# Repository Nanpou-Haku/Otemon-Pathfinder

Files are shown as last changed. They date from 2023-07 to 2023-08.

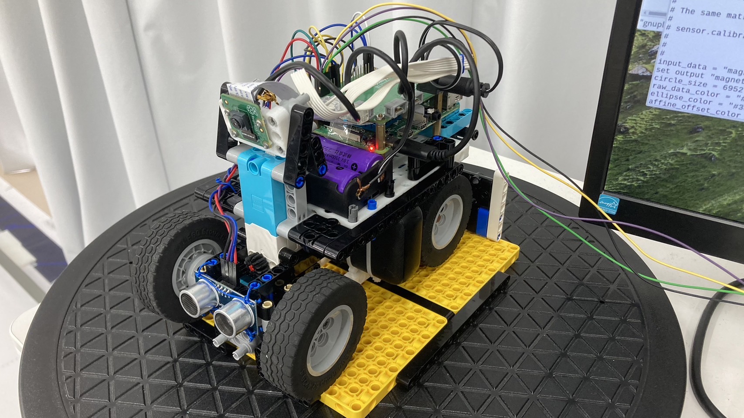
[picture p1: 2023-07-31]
IMG_1999.JPG

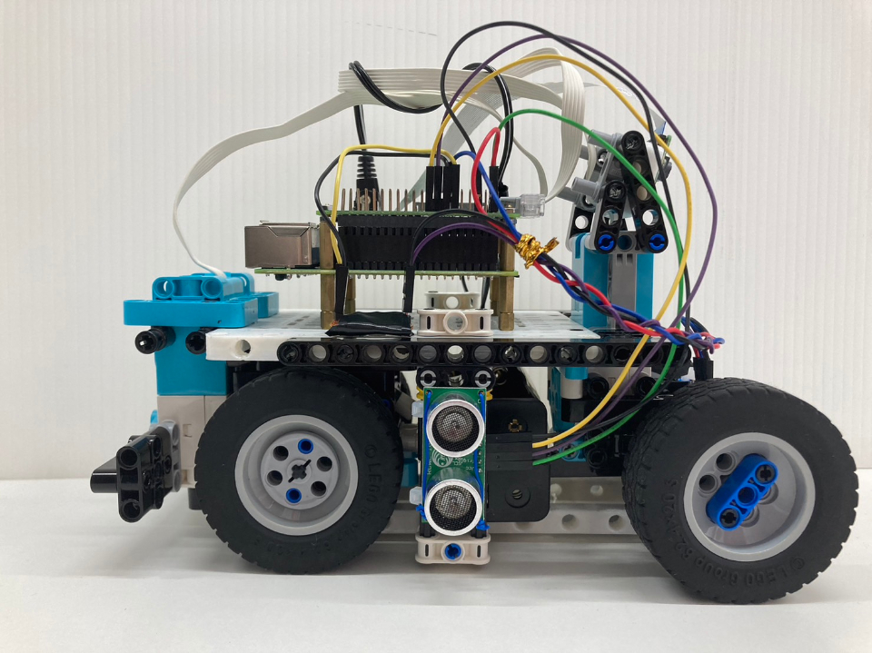
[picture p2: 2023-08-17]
v-photos/robot_right.jpg

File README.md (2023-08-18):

Otemon Pathfinder
====
このレポジトリには、WRO Japan 2023 FUTURE ENGINEERSの自動運転車に関するエンジニアリング資料(すべてのコードや資料など)が含まれています。
___

## 目次

* [自己紹介](#%E8%87%AA%E5%B7%B1%E7%B4%B9%E4%BB%8B)
* [ロボットについて](#%E3%83%AD%E3%83%9C%E3%83%83%E3%83%88%E3%81%AB%E3%81%A4%E3%81%84%E3%81%A6)
* [ハードウェア](#%E3%83%8F%E3%83%BC%E3%83%89%E3%82%A6%E3%82%A7%E3%82%A2)
    * [写真](#%E3%83%AD%E3%83%9C%E3%83%83%E3%83%88%E3%81%AE%E5%86%99%E7%9C%9F)
    * [設計図](#%E8%A8%AD%E8%A8%88%E5%9B%B3)
      * 回路図
      * 構図
      * ステアリング部分
    * [構成の理由](#%E3%81%93%E3%81%AE%E6%A7%8B%E6%88%90%E3%81%AE%E7%90%86%E7%94%B1)
* [ソフトウェア](#%E3%82%BD%E3%83%95%E3%83%88%E3%82%A6%E3%82%A7%E3%82%A2)
  * [使用OS](#%E4%BD%BF%E7%94%A8OS)
  * [プログラミング言語](#%E3%83%97%E3%83%AD%E3%82%B0%E3%83%A9%E3%83%9F%E3%83%B3%E3%82%B0%E8%A8%80%E8%AA%9E)
  * [アルゴリズム](#%E3%82%A2%E3%83%AB%E3%82%B4%E3%83%AA%E3%82%BA%E3%83%A0)
    * [前提](#%E5%89%8D%E6%8F%90%0D%0A)
    * [Open Challenge](#OpenChallenge)
    * [Obstacle Challenge](#ObstacleChallenge)

## 自己紹介

私たちは「Otemon Pathfinder」です。私たちのチームには3人のメンバーがいます。

- 安井　昌望
- 南方　博
- 藤村　昭允
  
（左から）

team_funny

## ロボットについて

私たちのロボットは車体をレゴのパーツで作っており、レゴのパーツで実現することができないものは3Dプリンターで部品を作り、レゴのパーツと互換性を持たせています。

robot

## ハードウェア

| デバイス |  | 用途 |
| :--: | :--:| :--: |
| Raspberry Pi 4B |  | プログラムの実行およびその処理 |
| BuildHat | | LEGOのモーターと接続し、Raspberry Piで制御 |
| Pi Camera V2 |  | 障害物認識、壁検知 |
| HC-SR04 |  | 超音波センサーは壁との距離を計測 前面:衝突を回避 側面:時計回り・半時計回りの判別 |
| Large Angular Motor |　 | 駆動 |
| Medium Angular Motor |  | 操舵 |
| 18650(3.6V, 2600mAh) |  | 電源供給 |
| Switch |  | ロボットの起動 |

### ロボットの写真

| Front | Back |
| -- | -- |
| robot_front | robot_back |

| Left | Right |
| -- | -- |
| robot_left | robot_right |

| Top | Bottom |
| -- | -- |
| robot_top | robot_bottom |

### 設計図
* **回路図**

diagram

* **構図**

blueprint

ディファレンシャルギアはただモーターからタイヤに動力を伝えるのではなく、モーターからリングギアを通して、ピニオンギアやサイドギアへ繋ぎ、タイヤに動力を伝えています。こうすることで、タイヤが両方とも何の負荷もかからずに走行した場合はリングギアが回転し、ピニオンギアは動きません。しかし、どちらか片方が動かない、もしくは負荷がかかった場合にはピニオンギアが作動し、もう片方のタイヤを余分に回転させます。こうすることで**タイヤの回転差を調整し、スムーズな走行が可能**になり、コートでカーブする際に効果を発揮します。

differential gear 

（ディファレンシャルギア）

* **ステアリング部分**

steering

### この構成の理由

1. トライ＆エラーのしやすさ：私たちはRaspberry Piの高い拡張性を活用することで、様々な種類のカメラモジュール、I2C接続センサー、GPIO制御を試しました。こうした豊富な選択肢を通じて、異なる手法やアプローチを試行し、最適解を求めていくことを可能にしました。

2. 最適な互換性：LEGOを選んだ理由は、**組み立てが容易で、ロボットの修理や新しい機構の追加が素早く行える**ためです。加えて、多様なパーツが利用でき、アイデアを迅速に形にできます。さらに、Raspberry Pi BuildHatを使用してLEGO SpikeのモーターをRaspberry Piで制御できる**高い互換性**があり、3Dプリンターを活用してLEGOと互換性のあるカスタムパーツを製作できるため、理想のロボットを作り上げるための自由度が高めました。

3. エネルギー効率とコスト：Lidarセンサーの代わりにカメラや超音波センサーを使っている理由は、**コストパフォーマンスや主な焦点である軽量設計**に貢献していること、通常、Lidarセンサーに比べ、カメラや超音波センサーは**低い消費電力**であり、エネルギー効率が良いです。

4. 安定した電力供給と柔軟性：18650電池4本をBuildHatに接続し、電源を供給することにしました。**スイッチを一度オンにするだけ電源を供給することができ、バッテリーの交換や管理が容易に行えるため、柔軟な運用が可能で、負荷の高い処理を実行する際にも安定した電力供給が保たれ、長時間の稼働においても安定性**が保たれることが期待されます。

## ソフトウェア

### 使用OS

私たちは既存のDebian BusterがベースとなったRaspberry Pi OSを使用しています。

### プログラミング言語

私たちのコードはすべて、Pythonで書かれています。

### アルゴリズム

* ### 前提

前提として、カメラの解像度は画像処理に大きく影響します。Pi Camera V2の場合、解像度と画素数は以下の表のようになります。

| 解像度 | 画素数 |
| :--: | :--: |
| 1920 × 1080 | 207万画素 |
| 1280 x 720 | 92万画素 |
| 640 x 480 | 30万画素 |

この表から分かるように、高解像度の場合、データ量が多く、リアルタイムで処理する際に処理に負荷がかかります。Future Engineersでは、3分以内に3周する速度とオブジェクトの認識の精度が求められるため、高解像度であると、処理能力が追いつかず、FPS(フレームレート)が下がり、画像データの更新が遅くなります。Open Challengeでは障害物を避ける必要がなく、壁のみの画像処理と超音波によるP制御より、解像度は640×480とし、Obstacle Challengeでは障害物と壁の画像処理が必要であるため、320×240としています。

* ### OpenChallenge

Open Challengeは、トラックに障害物がなく、中央の壁が変化することにより、セクションにより壁と壁の幅が変化するため、適応しながら、3周をするミッションです。このミッションの達成方法として、以下のアルゴリズムを考えました。

1. 障害物がないため、壁のしきい値の最小値と最大値の範囲を定義し、真ん中から下部をROI(関心領域)抽出・マスク処理(二値化)をしたあと、そのデータにオープニング処理(ノイズ除去、特徴抽出)を施す。

2. オープニング処理を施した画像の輪郭から壁の最大面積を算出する。

3. 画像の中央（ROI抽出した画像の左側、右側を切り取る）のみにし、中央に表示される壁の面積がある一定の値を超えるまで、ロボットの左右にある超音波センサー(HC-SR04)で左右の壁のちょうど中央になるようにP制御を用いて、トレースをする。

4. 中央に表示される壁の面積がある一定の値を超える条件が満たされた時、壁に近いので、左右の超音波センサーのうち、どちら側が壁からの距離が遠いか比較し、判別する。

5. 壁からの距離が遠い方で時計回りか反時計回りか判別できるので、その判別結果を用いて、時計回りなら右に、反時計回りなら左に曲がるようにステアリングを操作する。(この時、時計回りか反時計回りかを記憶し、２回目以降にその判断結果を用いる)

6. 1.~5.の動作を3周するまで繰り返す。

* ### ObstacleChallenge

Obstacle Challengeは、障害物を避けながら、3周をするミッションです。このミッションの達成方法として以下のアルゴリズムを考えました。

1. 赤色と緑色のしきい値の最小値と最大値の範囲を定義し、マスク処理をしたあと、そのデータにオープニング処理を施す。

2. オープニング処理を施した画像の輪郭から赤色と緑色の最大面積とその面積の重心を算出する。

detect

content

3. その最大面積を評価し、赤と緑、どちらの面積の方が大きいか、その面積は十分に大きいかという条件を満たすか判定する。(算出された面積が大きければ、大きいほどロボットに近いところにあるといえる)

4. ロボットの目の前にオブジェクトがある時(面積がある一定の値以上の条件)オブジェクトの色に応じて、ステアリングを操作し、回避を行う。

5. ここで、三分割されたマスク画像について、2.で算出された重心が赤なら左側の領域、緑なら右側の領域に入った時、オブジェクトは回避できたと判断する。

6. 4.、5.の間にかかった時間（回避に要した時間)を算出しておき、それを元に今度は逆向きにステアリングを操作し、ロボットを元の位置に戻す。

7. 1.~6.の動作を3周するまで繰り返す。

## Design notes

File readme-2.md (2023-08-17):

Otemon Pathfinder
====
このレポジトリには、WRO Japan 2023 FUTURE ENGINEERSの自動運転車に関するエンジニアリング資料(すべてのコードや資料など)が含まれています。
___

## 目次

* [自己紹介](#%E8%87%AA%E5%B7%B1%E7%B4%B9%E4%BB%8B)
* [ロボットについて](#%E3%83%AD%E3%83%9C%E3%83%83%E3%83%88%E3%81%AB%E3%81%A4%E3%81%84%E3%81%A6)
* [ハードウェア](#%E3%83%8F%E3%83%BC%E3%83%89%E3%82%A6%E3%82%A7%E3%82%A2)
    * [写真](#%E3%83%AD%E3%83%9C%E3%83%83%E3%83%88%E3%81%AE%E5%86%99%E7%9C%9F)
    * [設計図](#%E8%A8%AD%E8%A8%88%E5%9B%B3)
      * 回路図
      * 構図
      * ステアリング部分
    * [構成の理由](#%E3%81%93%E3%81%AE%E6%A7%8B%E6%88%90%E3%81%AE%E7%90%86%E7%94%B1)
* [ソフトウェア](#%E3%82%BD%E3%83%95%E3%83%88%E3%82%A6%E3%82%A7%E3%82%A2)
  * [使用OS](#%E4%BD%BF%E7%94%A8OS)
  * [プログラミング言語](#%E3%83%97%E3%83%AD%E3%82%B0%E3%83%A9%E3%83%9F%E3%83%B3%E3%82%B0%E8%A8%80%E8%AA%9E)
  * [アルゴリズム](#%E3%82%A2%E3%83%AB%E3%82%B4%E3%83%AA%E3%82%BA%E3%83%A0)
    * [前提](#%E5%89%8D%E6%8F%90%0D%0A)
    * [Open Challenge](#OpenChallenge)
    * [Obstacle Challenge](#ObstacleChallenge)

## 自己紹介

私たちのチーム「Otemon Pathfinder」には3人のメンバーがいます。

- 安井　昌望
- 南方　博
- 藤村　昭允
  
（左から）

team_funny

## ロボットについて

私たちのロボットは、ハードウェアもソフトウェアも無駄のない設計にこだわりました。
ハードウェアの面では汎用的なレゴのパーツにより高いカスタマイズ性を担保しつつ、専用設計したパーツを組み合わせることで無駄がない構造の実現に成功しました。
ソフトウェアの面では再利用性のあるクラスにより汎用的で非冗長的な処理をしつつ、比較的単純なアルゴリズムで保守性と可読性のあるコードの実現に成功しました。

robot

## ハードウェア

| デバイス |  | 用途 |
| :--: | :--:| :--: |
| Raspberry Pi 4B |  | プログラムの実行およびその処理 |
| BuildHat | | LEGOのモーターと接続し、Raspberry Piで制御 |
| Pi Camera V2 |  | 障害物認識、壁検知 |
| HC-SR04 |  | 超音波センサーは壁との距離を計測 前面:衝突を回避 側面:時計回り・半時計回りの判別 |
| Large Angular Motor |　 | 駆動 |
| Medium Angular Motor |  | 操舵 |
| 18650(3.6V, 2600mAh) |  | 電源供給 |
| Switch |  | ロボットの起動 |

### ロボットの写真

| Front | Back |
| -- | -- |
| robot_front | robot_back |

| Left | Right |
| -- | -- |
| robot_left | robot_right |

| Top | Bottom |
| -- | -- |
| robot_top | robot_bottom |

### 設計図
* **回路図**

diagram

* **構図**

blueprint

ディファレンシャルギアはただモーターからタイヤに動力を伝えるのではなく、モーターからリングギアを通して、ピニオンギアやサイドギアへ繋ぎ、タイヤに動力を伝えています。こうすることで、タイヤが両方とも何の負荷もかからずに走行した場合はリングギアが回転し、ピニオンギアは動きません。しかし、どちらか片方が動かない、もしくは負荷かかかった場合にはピニオンギアが作動し、もう片方のタイヤを余分に回転させます。こうすることで**タイヤの回転差を調整し、スムーズな走行が可能**になり、コート上でカーブする際に効果を発揮します。

differential gear 

（ディファレンシャルギア）

* **ステアリング部分**

steering

### この構成の理由

1. トライ＆エラーのしやすさ：私たちはRaspberry Piの高い拡張性を活用することで、様々な種類のカメラモジュール、i2c接続センサ、gpio制御を試し、多くの手法から最適解を求めていくことを可能にしました。

2. 最適な互換性：LEGOを選んだ理由は、**組み立てが容易で、ロボットの修理や新しい機構の追加が素早く行える**ためです。加えて、多様なパーツが利用でき、アイデアを迅速に形にできます。さらに、Raspberry Pi BuildHatを使用してLEGO SpikeのモーターをRaspberry Piで制御できる**高い互換性**があり、3Dプリンターを活用してLEGOと互換性のあるカスタムパーツを製作できるため、理想のロボットを作り上げるための自由度を高めました。

3. エネルギー効率とコスト：Lidarセンサーの代わりにカメラや超音波センサーを使っている理由は、**コストパフォーマンスや主な焦点である軽量設計**に貢献していること、通常、Lidarセンサーに比べ、カメラや超音波センサーは**低い消費電力**であり、エネルギー効率が良いです。

4. 安定した電力供給と柔軟性：18650電池4本を BuildHatに接続し、電源を供給することにしました。**スイッチを一度オンにするだけで電源を供給することができ、バッテリーの交換や管理が容易に行える**ため、**柔軟な運用**が可能で、**電力供給の安定性が増し、長時間稼働する際にも安定性**が保たれることが期待されます。

## ソフトウェア

### 使用OS

私たちはRaspberry Pi OSを使用しています。

### プログラミング言語

私たちのコードはすべて、Pythonで書かれています。

### アルゴリズム

* ### 前提

前提として、カメラの解像度は画像処理に大きく影響します。Pi Camera V2の場合、解像度と画素数は以下の表のようになります。

| 解像度 | 画素数 |
| :--: | :--: |
| 1920 × 1080 | 207万画素 |
| 1280 x 720 | 92万画素 |
| 640 x 480 | 30万画素 |

この表から分かるように、高解像度の場合、データ量が多く、リアルタイムで処理する際に処理に負荷がかかります。Future Engineersでは、3分以内に3周する速度とオブジェクトの認識の精度が求められるため、高解像度であると、処理能力が追いつかず、FPS(フレームレート)が下がり、画像データの更新が遅くなります。Open Challengeでは障害物を避ける必要がなく、壁のみの画像処理と超音波によるP制御より、解像度は640×480とし、Obstacle Challengeでは障害物と壁の画像処理が必要であるため、320×240としています。

* ### OpenChallenge

Open Challengeは、トラックに障害物がなく、中央の壁が変化することにより、セクションにより壁と壁の幅が変化するため、適応しながら、3周をするミッションです。このミッションの達成方法として、以下のアルゴリズムを考えました。

1. 障害物がないため、壁のしきい値の最小値と最大値の範囲を定義し、真ん中から下部をROI(関心領域)抽出・マスク処理(二値化)をしたあと、そのデータにオープニング処理(ノイズ除去、特徴抽出)を施す。

2. オープニング処理を施した画像の輪郭から壁の最大面積を算出する。

3. 画像の中央（ROI抽出した画像の左側、右側を切り取る）のみにし、中央に表示される壁の面積がある一定の値を超えるまで、ロボットの左右にある超音波センサー(HC-SR04)で左右の壁のちょうど中央になるようにP制御を用いて、トレースをする。

4. 中央に表示される壁の面積がある一定の値を超える条件が満たされた時、壁に近いので、左右の超音波センサーのうち、どちら側が壁からの距離が遠いか比較し、判別する。

5. 壁からの距離が遠い方で時計回りか反時計回りか判別できるので、その判別結果を用いて、時計回りなら右に、反時計回りなら左に曲がるようにステアリングを操作する。(この時、時計回りか反時計回りかを記憶し、２回目以降にその判断結果を用いる)

6. 1.~5.の動作を3周するまで繰り返す。

* ### ObstacleChallenge

Obstacle Challengeは、障害物を避けながら、3周をするミッションです。このミッションの達成方法として以下のアルゴリズムを考えました。

1. 赤色と緑色のしきい値の最小値と最大値の範囲を定義し、マスク処理をしたあと、そのデータにオープニング処理を施す。

2. オープニング処理を施した画像の輪郭から赤色と緑色の最大面積とその面積の重心を算出する。

detect

content

3. その最大面積を評価し、赤と緑、どちらの面積の方が大きいか、その面積は十分に大きいかという条件を満たすか判定する。(算出された面積が大きければ、大きいほどロボットに近いところにあるといえる)

4. ロボットの目の前にオブジェクトがある時(面積がある一定の値以上の条件)オブジェクトの色に応じて、ステアリングを操作し、回避を行う。

5. ここで、三分割されたマスク画像について、2.で算出された重心が赤なら左側の領域、緑なら右側の領域に入った時、オブジェクトは回避できたと判断する。

6. 4.、5.の間にかかった時間（回避に要した時間)を算出しておき、それを元に今度は逆向きにステアリングを操作し、ロボットを元の位置に戻す。

7. 1.~6.の動作を3周するまで繰り返す。

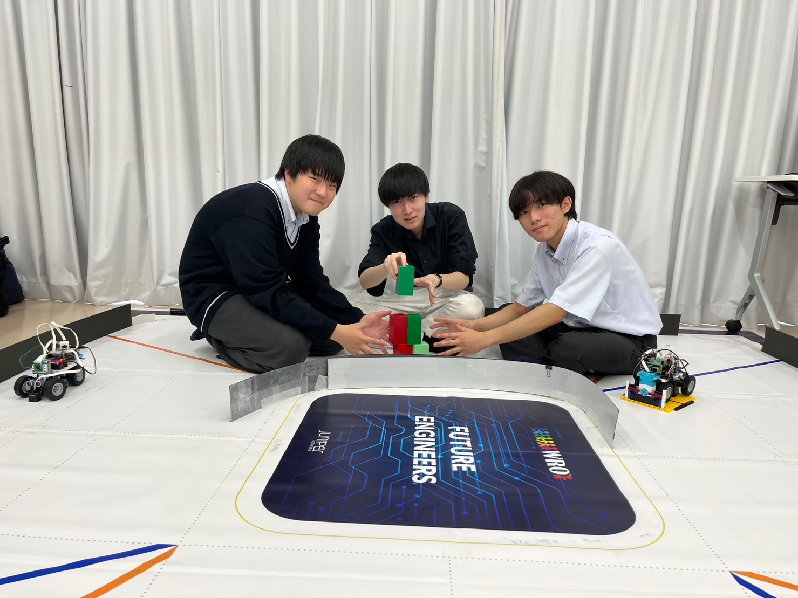
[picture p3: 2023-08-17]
t-photos/team_funny.jpg

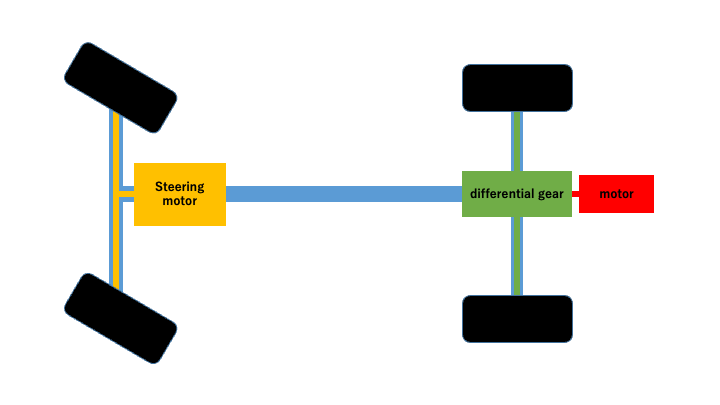
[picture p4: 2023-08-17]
models/robot_blueprint.png

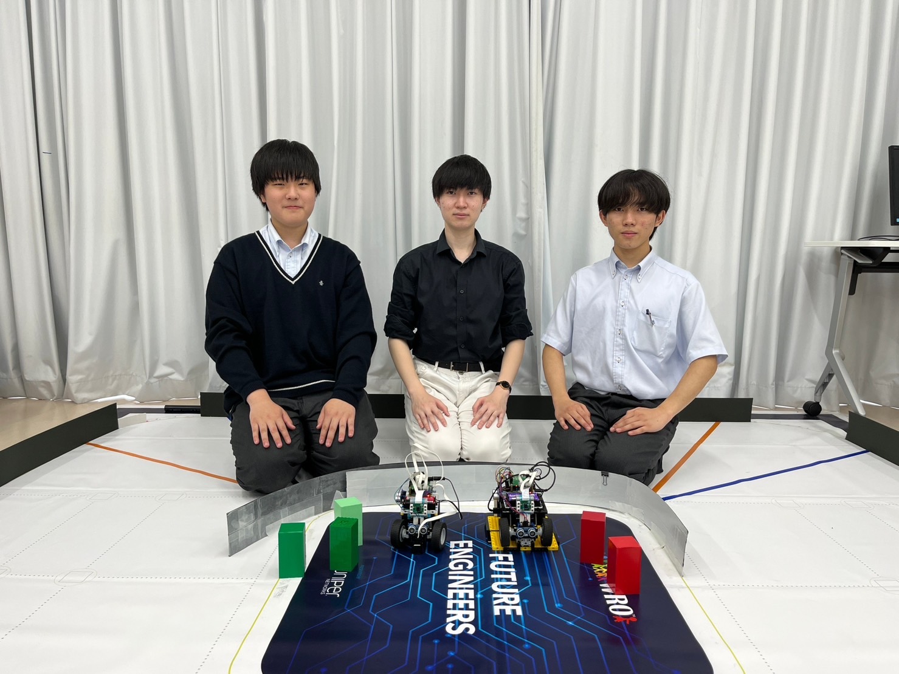
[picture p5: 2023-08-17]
t-photos/team_official.jpg

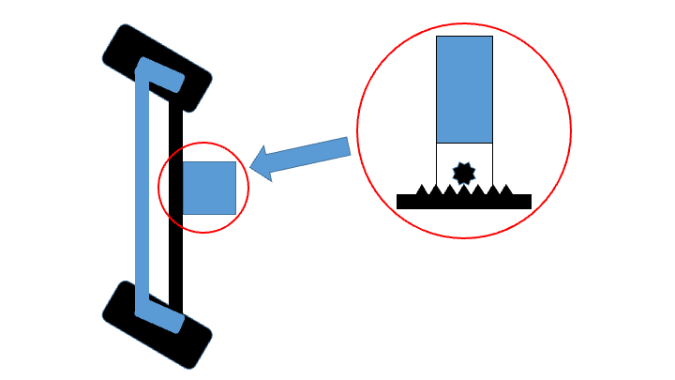
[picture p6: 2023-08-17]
models/robot_steering.png

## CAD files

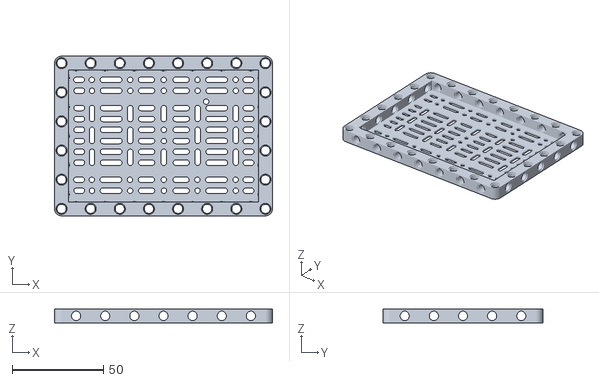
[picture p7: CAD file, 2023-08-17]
models/raspberry-lego-maker-plate_v4.stl
119.8 x 87.8 x 7.75

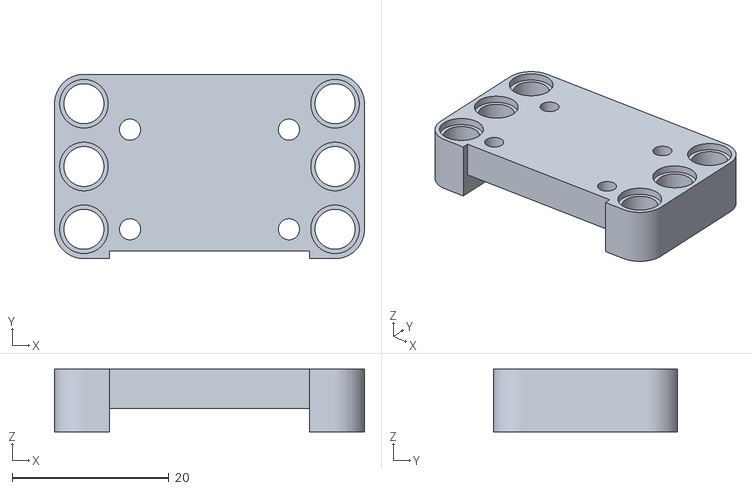
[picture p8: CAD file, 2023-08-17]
models/camera2.stl
39.5 x 23.5 x 8.00

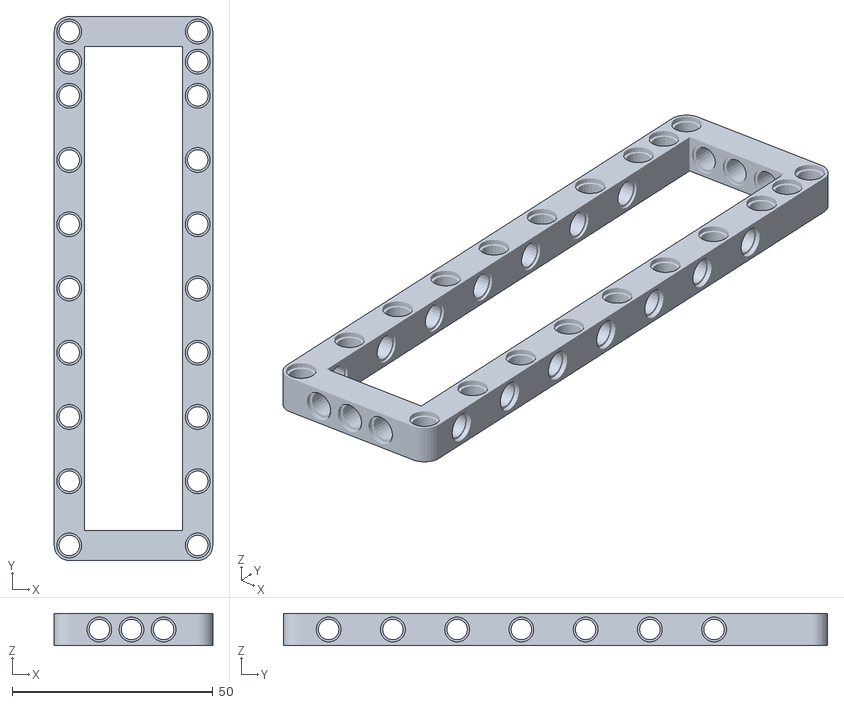
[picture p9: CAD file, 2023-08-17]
models/robot_under.stl
39.5 x 135.5 x 8.00

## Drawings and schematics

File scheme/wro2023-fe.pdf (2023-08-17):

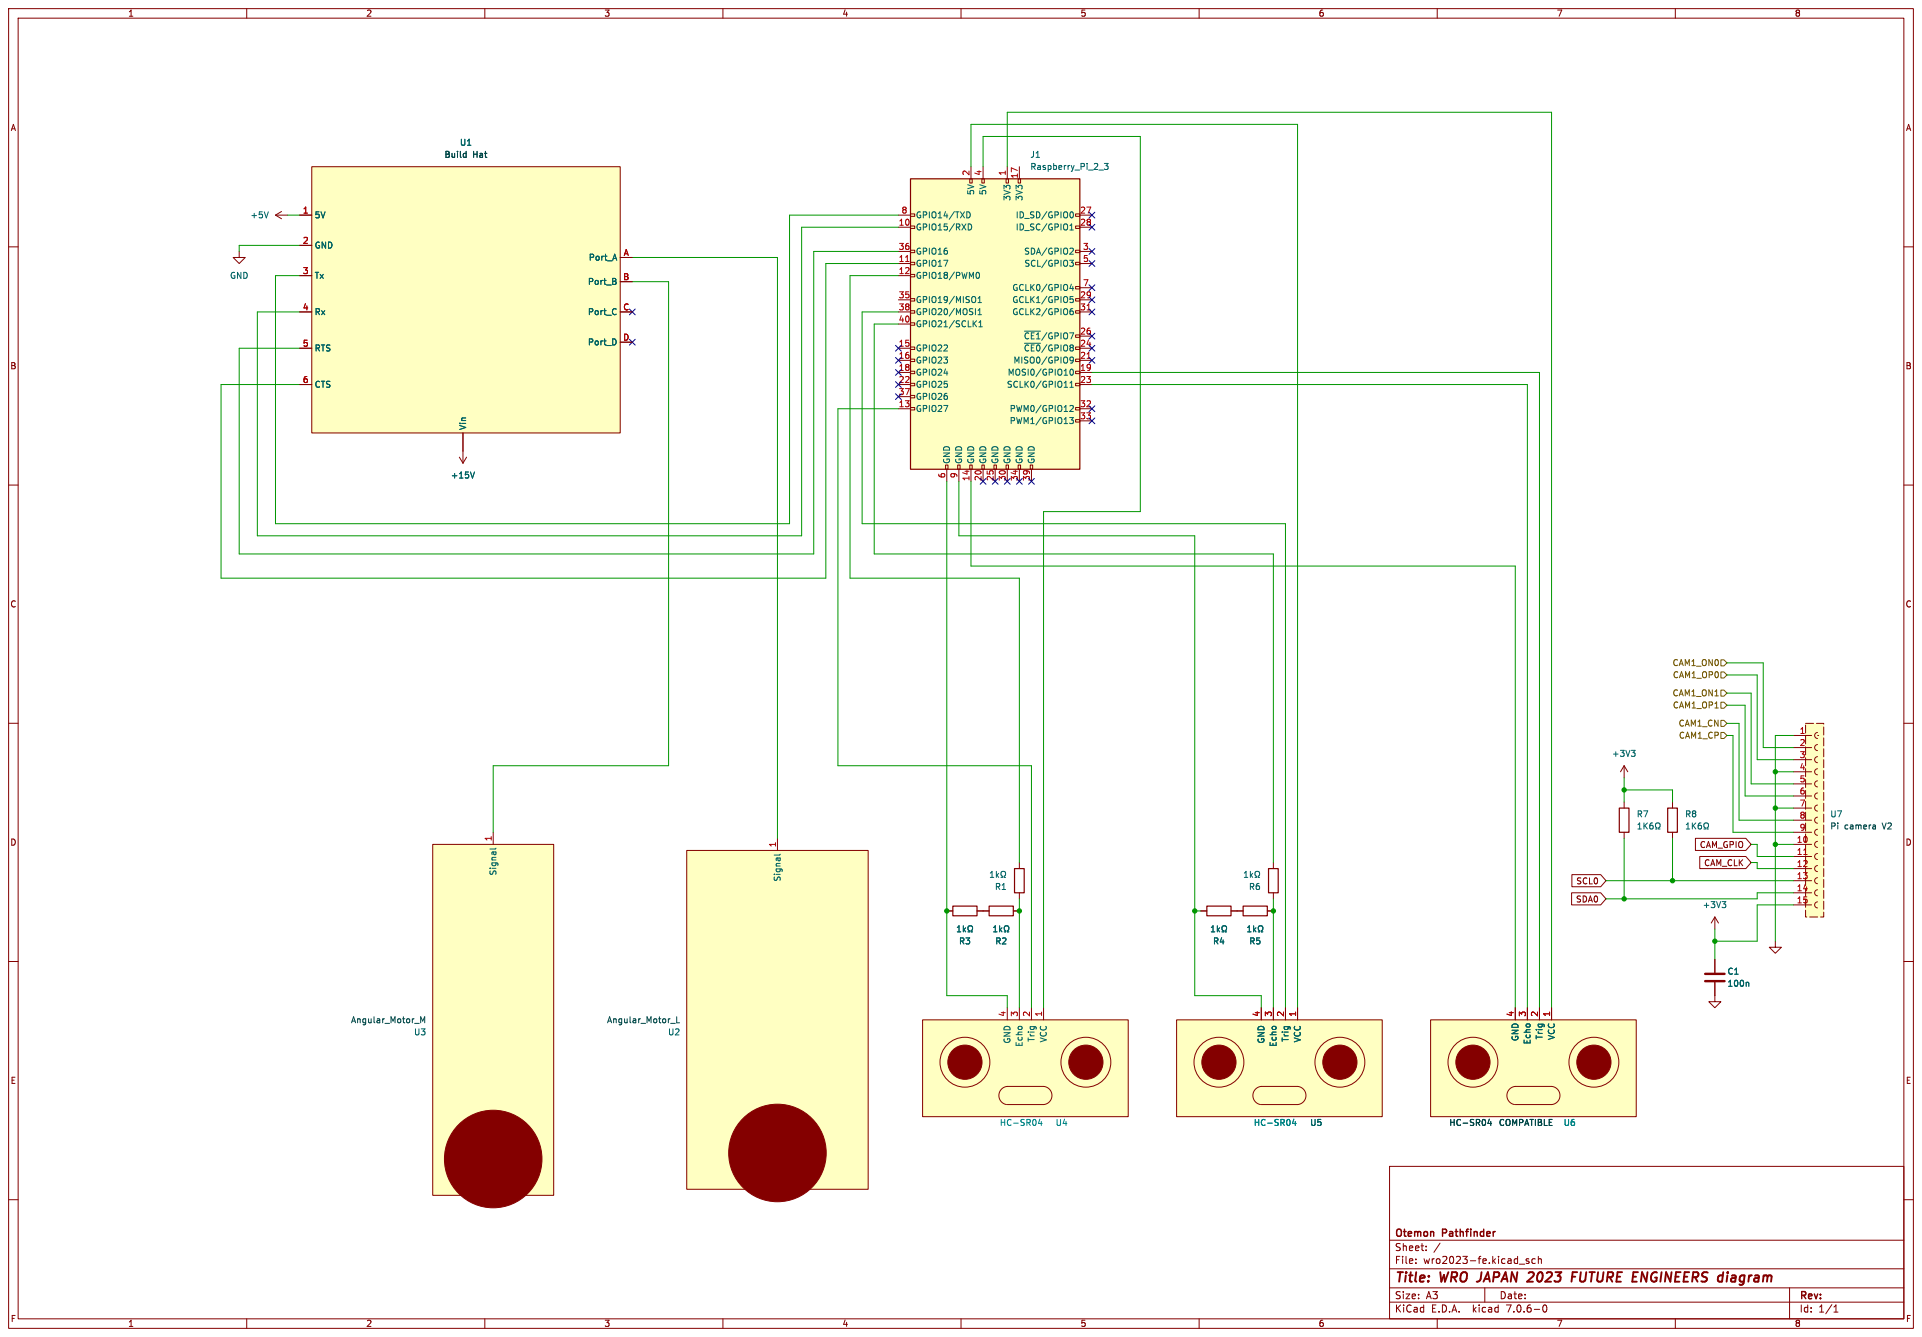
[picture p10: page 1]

Id: 1/1 Title: WRO JAPAN 2023 FUTURE ENGINEERS diagram

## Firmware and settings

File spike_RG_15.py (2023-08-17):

import time
import atexit
import picamera
import picamera.array
import RPi.GPIO as GPIO
from dataclasses import dataclass
import cv2
import numpy as np
from buildhat import Motor, ForceSensor
import copy
import math

@dataclass
class ColorDatas:
    color      : int = 0
    lower      : np.ndarray = None
    upper      : np.ndarray = None
    mask       : np.ndarray = None
    dst        : np.ndarray = None
    dstt       : np.ndarray = None
    res        : np.ndarray = None
    contour    : np.ndarray = None
    hierarchy  : np.ndarray = None
    maxContour : int = None
    area       : int = None
    moments    : dict = None
    
#pin
trig_front = 27
echo_front = 18
trig_side = 20
echo_side = 21

#connect
motor = Motor('A')
steering = Motor('B')
left = -70
right = 70

#color
green = ColorDatas()
red = ColorDatas()
red2 = ColorDatas()
blue = ColorDatas()
black = ColorDatas()

#camera
camera = picamera.PiCamera()
wide, high = (320, 240)
frame = 10

sig_off = 0
dig_on = 0
start = 0
end = 0
total = 0
clock = 0
direction = 0
counter = 0
surf = 0
blue.area = 0
degree = 0

first = True
waitPls = True

poleFlag = False
blueFlag = False
startFlag = False

#Hiroshi
def init():
    GPIO.setwarnings(False)
    GPIO.setmode(GPIO.BCM)              
    GPIO.setup(trig_front, GPIO.OUT)          
    GPIO.setup(echo_front, GPIO.IN)
    GPIO.setup(trig_side, GPIO.OUT)          
    GPIO.setup(echo_side, GPIO.IN)
    
    blue.lower = np.array([104, 85, 0])
    blue.upper = np.array([170, 255, 163])
    blue.color = "blue"
    
    green.lower = np.array([40, 60, 40])
    green.upper = np.array([80, 255, 255])
    green.color = "green"
    
    red.lower = np.array([160, 60, 50])
    red.upper = np.array([179, 255, 255])
    red.color = "red"

    red2.lower = np.array([0, 255, 50])
    red2.upper = np.array([30, 255, 255])   
    red2.color = "red"
    
    black.lower = np.array([0, 0, 0])
    black.upper = np.array([50, 225, 110])
    black.color = "black"
    
    camera.rotation = 180
    camera.resolution = (wide, high)
    camera.framerate = frame
    
def UpdateCamera(stream, kernel):
    #camera
    camera.capture(stream, 'bgr', use_video_port=True)
    hsv = cv2.cvtColor(stream.array, cv2.COLOR_BGR2HSV)
    
    hsvline = cv2.cvtColor(stream.array, cv2.COLOR_BGR2HSV)
    blind = cv2.rectangle(hsvline, (0, 0), (320, 120), (100, 100, 100), -1)
    
    hsvblack = cv2.cvtColor(stream.array, cv2.COLOR_BGR2HSV)
    black_blind1 = cv2.rectangle(hsvblack, (0, 0), (320, 100), (240, 240, 240), -1)
    black_blind2 = cv2.rectangle(black_blind1, (0, 0), (20, 240), (240, 240, 240), -1)
    black_blind3 = cv2.rectangle(black_blind2, (300, 0), (320, 240), (240, 240, 240), -1)
    
    #マスク処理
    green.mask = cv2.inRange(hsv, green.lower, green.upper)
    red.mask = cv2.inRange(hsv, red.lower, red.upper)
    red2.mask = cv2.inRange(hsv, red2.lower, red2.upper)
    red.mask = red.mask + red2.mask
    
    blue.mask = cv2.inRange(hsvline, blue.lower, blue.upper)
    black.mask = cv2.inRange(hsvblack, black.lower, black.upper)
    
    #オープニング
    green.dst = cv2.erode(green.mask, kernel, iterations=1)
    green.dstt = cv2.dilate(green.dst, kernel, iterations=1)
    red.dst = cv2.erode(red.mask, kernel, iterations=1)
    red.dstt = cv2.dilate(red.dst, kernel, iterations=1)
    
    blue.dst = cv2.erode(blue.mask, kernel, iterations=1)
    blue.dstt = cv2.dilate(blue.dst, kernel, iterations=1)
    black.dst = cv2.erode(black.mask, kernel, iterations=1)
    black.dstt = cv2.dilate(black.dst, kernel, iterations=1)
    
    #合成
    green.res = cv2.bitwise_and(stream.array, stream.array, mask=green.dstt)
    red.res = cv2.bitwise_and(stream.array, stream.array, mask=red.dstt)
    
    blue.res = cv2.bitwise_and(stream.array, stream.array, mask=blue.dstt)
    black.res = cv2.bitwise_and(stream.array, stream.array, mask=black.dstt)
    
    #輪郭検出
    green.contour, green.hierarchy = cv2.findContours(green.mask, cv2.RETR_EXTERNAL, cv2.CHAIN_APPROX_SIMPLE)
    red.contour, red.hierarchy = cv2.findContours(red.mask, cv2.RETR_EXTERNAL, cv2.CHAIN_APPROX_SIMPLE)
    
    blue.contour, blue.hierarchy = cv2.findContours(blue.mask, cv2.RETR_EXTERNAL, cv2.CHAIN_APPROX_SIMPLE)
    black.contour, black.hierarchy = cv2.findContours(black.mask, cv2.RETR_EXTERNAL, cv2.CHAIN_APPROX_NONE)
    
    #分割線描画
    cv2.line(green.res, (41, 0), (41,240), (255, 215, 0), 1)
    cv2.line(green.res, (280, 0), (280,240), (255, 215, 0), 1)
    cv2.line(red.res, (41, 0), (41,240), (255, 215, 0), 1)
    cv2.line(red.res, (280, 0), (280,240), (255, 215, 0), 1)

#Fujimura
def situation():
    stream = picamera.array.PiRGBArray(camera)
    kernel = cv2.getStructuringElement(cv2.MORPH_RECT, (3,3))
    UpdateCamera(stream, kernel)
    
    if (len(green.contour) != 0):
        green.maxContour = max(green.contour, key = lambda x: cv2.contourArea(x))
        green.area = cv2.contourArea(green.maxContour)
        green.moments = cv2.moments(green.maxContour)
    
    if (len(red.contour) != 0):
        red.maxContour = max(red.contour, key = lambda x: cv2.contourArea(x))
        red.area = cv2.contourArea(red.maxContour)
        red.moments = cv2.moments(red.maxContour)
    
    if (len(black.contour) != 0):
        black.maxContour = max(black.contour, key = lambda x: cv2.contourArea(x))
        black.area = cv2.contourArea(black.maxContour)
        black.moments = cv2.moments(black.maxContour)
    
    else:
        green.area = 0
        red.area = 0
        black.area = 0
    
def situationBlue():
    stream = picamera.array.PiRGBArray(camera)
    kernel = cv2.getStructuringElement(cv2.MORPH_RECT, (3,3))
    UpdateCamera(stream, kernel)
    
    if (len(blue.contour) != 0):
        blue.maxContour = max(blue.contour, key = lambda x: cv2.contourArea(x))
        blue.area = cv2.contourArea(blue.maxContour)
        blue.moments = cv2.moments(blue.maxContour)
    
    else:
        blue.area = 0
        
    return blue.area
    
def CameraShow(stream, kernel):
    #表示
    cv2.imshow("frame", stream.array)
    cv2.imshow("Green", green.res)
    cv2.imshow("Red", red.res)
    cv2.imshow("Blue", blue.res)
    cv2.imshow("black", black.res)
    cv2.waitKey(1)
    stream.seek(0)
    stream.truncate()

#Hiroshi
def fini():
    motor.stop()
    cv2.destroyAllWindows()

#Hiroshi
def motorMove(motor, nowPosition, goPosition):
    global startFlag
    if(nowPosition != goPosition):
        motor.run_to_position(goPosition)
        nowPosition = goPosition
        
        global start, end, total

        if nowPosition != 0:
            start = time.perf_counter()

        elif (startFlag):
            end = time.perf_counter()
            total = end - start
            
            print("total =", total)
            
    startFlag = True
            
    return nowPosition

#Hiroshi
def motorPosition(color, left, center, right):
    cube_x = int(color.moments["m10"] / color.moments["m00"])
    cube_y = int(color.moments["m01"] / color.moments["m00"])
    cv2.circle(color.dstt, (cube_x, cube_y), 2, 100, 2, 4)
    cv2.circle(color.res, (cube_x, cube_y), 2, 100, 2, 4)
    
    global end
    
    if 0 <= cube_x <= 40:
        position = left
    elif 41 <= cube_x <= 280:
        position = center                   
    elif 281 <= cube_x <= 320:
        position = right

    return position

#Yasui
def read_distance_front():
    GPIO.output(trig_front, GPIO.HIGH)
    time.sleep(0.00001)
    GPIO.output(trig_front, GPIO.LOW)
    
    sig_on_front = 0
    sig_off_front = 0
    
    while GPIO.input(echo_front) == GPIO.LOW:
        sig_off_front = time.time()
    while GPIO.input(echo_front) == GPIO.HIGH:
        sig_on_front = time.time()
     
    duration_front = sig_on_front - sig_off_front
    distance_front = duration_front * 34000 / 2
    return distance_front

#Yasui
def read_distance_side():
    GPIO.output(trig_side, GPIO.HIGH)
    time.sleep(0.00001)
    GPIO.output(trig_side, GPIO.LOW)
    
    sig_on_side = 0
    sig_off_side = 0
    
    while GPIO.input(echo_side) == GPIO.LOW:
        sig_off_side = time.time()
    while GPIO.input(echo_side) == GPIO.HIGH:
        sig_on_side = time.time()
     
    duration_side = sig_on_side - sig_off_side
    distance_side = duration_side * 34000 / 2
    return distance_side

def distanceTraceMove(motor, nowPosition, goPosition):
    if(nowPosition != goPosition):
        motor.run_to_position(goPosition)
        nowPosition = goPosition
    
    return nowPosition

#Yasui
def distanceMove(steering, nowPosition, left):
    cm_front = read_distance_front()
    cm_side = read_distance_side()
    global pole, counter, blueFlag, poleFlag, first, waitPls
    
    stream = picamera.array.PiRGBArray(camera)
    kernel = cv2.getStructuringElement(cv2.MORPH_RECT, (3,3))
    
    if first is True:
        if cm_front < 40:
            print("first avoid")
            motor.stop()
            situation()
            UpdateCamera(stream, kernel)
            nowPosition = pointDetect(nowPosition, cm_side)
            CameraShow(stream, kernel)
        
        else:
            motor.start(30)
            print("first")
            
            if blueFlag is False and waitPls is True:
                cm_side = read_distance_side()
                time.sleep(0.05)
                print("------")
                print("cm_side =", cm_side)
                print("tyuppatyappusu")
    
                if cm_side <= 30:
                    nowPosition = distanceTraceMove(steering, nowPosition, -30)
        
                elif 30 < cm_side < 40:
                    nowPosition = distanceTraceMove(steering, nowPosition, 0)
        
                elif 40 <= cm_side <= 80:
                    nowPosition = distanceTraceMove(steering, nowPosition, 30)
                    
                elif 80 < cm_side:
                    nowPosition = distanceTraceMove(steering, nowPosition, 0)
    
    elif poleFlag and blueFlag:
        if cm_front < 40:
            motor.stop()
            situation()
            UpdateCamera(stream, kernel)
            nowPosition = pointDetect(nowPosition, cm_side)
            CameraShow(stream, kernel)
        
        else:
            motor.start(30)
            
    else:
        motor.start(30)
        print("blueFlag =", blueFlag)
        if blueFlag is False and waitPls is True:
            cm_side = read_distance_side()
            time.sleep(0.05)
            print("------")
            print("cm_side =", cm_side)
            print("nupepeppepepepepe")
        
            if cm_side <= 30:
                nowPosition = distanceTraceMove(steering, nowPosition, -30)
        
            elif 30 < cm_side < 40:
                nowPosition = distanceTraceMove(steering, nowPosition, 0)
        
            elif 40 <= cm_side <= 80:
                nowPosition = distanceTraceMove(steering, nowPosition, 30)
            
            elif 80 < cm_side:
                nowPosition = distanceTraceMove(steering, nowPosition, 0)
            
    return nowPosition

#Fujimura
def avoid(nowPosition):
    if poleFlag and blueFlag:
        print("ignore")
        nowPosition = distanceMove(steering, nowPosition, left)
        
    else:
        situationBlue()
        
        #緑あり
        if (len(green.contour) != 0):
            green.maxContour = max(green.contour, key = lambda x: cv2.contourArea(x))
            green.area = cv2.contourArea(green.maxContour)
            green.moments = cv2.moments(green.maxContour)
            #赤あり
            if (len(red.contour) != 0):
                red.maxContour = max(red.contour, key = lambda x: cv2.contourArea(x))
                red.area = cv2.contourArea(red.maxContour)
                red.moments = cv2.moments(red.maxContour)
                #緑が近いなら緑を優先
                if red.area < green.area and 1200 < green.area < 9000:
                    if green.moments["m00"] != 0:
                       goPosition = motorPosition(green, left, left, 0)
                       nowPosition = motorMove(steering, nowPosition, goPosition)
                       lineDetect()
            
                #赤が近いなら赤を優先
                elif green.area < red.area and 1200 < red.area < 9000:
                    if red.moments["m00"] != 0:
                        goPosition = motorPosition(red, 0, right, right)
                        nowPosition = motorMove(steering, nowPosition, goPosition)
                        lineDetect()
 
                else:
                    nowPosition = distanceMove(steering, nowPosition, left)
                    lineDetect()
        
            #緑あり赤なし
            elif 1200 < green.area < 9000:
                if green.moments["m00"] != 0:
                    goPosition = motorPosition(green, left, left, 0)
                    nowPosition = motorMove(steering, nowPosition, goPosition)
                    lineDetect()
            
            else:
                nowPosition = distanceMove(steering, nowPosition, left)
                lineDetect()
    
        #緑なし赤あり
        elif (len(red.contour) != 0):
            red.maxContour = max(red.contour, key = lambda x: cv2.contourArea(x))
            red.area = cv2.contourArea(red.maxContour)
            red.moments = cv2.moments(red.maxContour)
            if 1200 < red.area < 9000:
                if red.moments["m00"] != 0:
                    goPosition = motorPosition(red, 0, right, right)
                    nowPosition = motorMove(steering, nowPosition, goPosition)
                    lineDetect()

            else:
                nowPosition =  distanceMove(steering, nowPosition, left)
                lineDetect()

        else:
            nowPosition = distanceMove(steering, nowPosition, left)
            lineDetect()

    return nowPosition

#Fujimura
def back(nowPosition, color):
    global total, clock, counter, surf, blueFlag, poleFlag, waitPls
    
    poleFlag = True
    waitPls = False
    steering.run_to_position(0)
    time.sleep(1.5)
    
    if color == "red":
        steering.run_to_position(-70)

    elif color == "green":
        steering.run_to_position(70)
    
    situationBlue()
    lineDetect()
    
    print("------")
    print("poleFlag =", poleFlag)
    print("blueFlag =", blueFlag)
    
    time.sleep(total*0.75)
    steering.run_to_position(0)

    time.sleep(2)
    
    total = 0
    clock = 0
    waitPls = True
    
def lineDetect():
    global blueFlag, poleFlag
    
    if poleFlag:
        if 500 <= blue.area:
            blueFlag = True
            print("------")
            print("Detect line")
            print("blueArea =", blue.area)
            print("poleFlag =", poleFlag)
            print("blueFlag =", blueFlag)
        
    else:
        print("------")
        print("poleFlag =", poleFlag)
        print("blueFlag =", blueFlag)
        
def pointDetect(nowPosition, cm_side):
    global degree
    cv2.drawContours(black.res, black.maxContour, -1, (255, 0, 0), 2)
    
    lx, ly = (float("inf"), float("inf"))
    rx, ry = (float("-inf"), float("-inf"))
    
    for contour in black.maxContour:
        for point in contour:
            x = point.item(0)
            y = point.item(1)
            
            if x < lx or (x == lx and y > ly):
                lx, ly = (x, y)
            
            if x > rx or (x == rx and y > ry):
                rx, ry = (x, y)
                
    if lx != float("inf") and ly != float("inf"):
        cv2.circle(black.res, (lx, ly), 5, (0, 0, 255), -1)
    
    if rx != float("-inf") and ry != float("-inf"):
        cv2.circle(black.res, (rx, ry), 5, (0, 255, 0), -1)
    
    tanh = abs(ly - ry)
    
    black_degree = (math.degrees(math.atan2(tanh, 280)))
    
    degree = (30/11 * black_degree) - 1
    
    print("------")
    
    if ry <= ly:
        degree = -1*degree

    return judgeDegree(nowPosition, cm_side)

def judgeDegree(nowPosition, cm_side):
    global poleFlag, blueFlag, first
    
    print("degree =", degree)
    if 4 <= degree:
        steering.run_to_position(40)
        motor.start(20)
        
    elif degree <= 0:
        steering.run_to_position(-40)
        motor.start(20)
        
    elif 0 < degree < 4:
        steering.run_to_position(0)
        motor.stop()
        print("ok")
        
        if cm_side >= 100:
            print("OrangeTyepe")
            print("cm_side =", cm_side)
            direction = 0 #0=cw 1=ccw/acw
            motor.run_for_seconds(1.3, 70)
            time.sleep(0.1)
            motor.run_for_seconds(0.5, -70)
            steering.run_to_position(-75)
            motor.run_for_seconds(2, -70)
            steering.run_to_position(0)
            motor.run_for_seconds(1.2, -100)
            time.sleep(0.1)
            situation()
            
            poleFlag = False
            blueFlag = False
            first = False
            
            nowPosition = motorMove(steering, nowPosition, 0)
            
        else:
            print("BlueTyepe")
            print("cm_side =", cm_side)
            direction = 1
            motor.run_for_seconds(1.3, 70)
            time.sleep(0.1)
            motor.run_for_seconds(0.5, -70)
            steering.run_to_position(75)
            motor.run_for_seconds(2, -70)
            steering.run_to_position(0)
            motor.run_for_seconds(1.2, -100)
            time.sleep(0.1)
            situation()
            
            poleFlag = False
            blueFlag = False
            first = False
            
            nowPosition = motorMove(steering, nowPosition, 0)
    
    return nowPosition

#Fujimura
def main():
    nowPosition = motorMove(steering, -1, 0)
    stream = picamera.array.PiRGBArray(camera)
    kernel = cv2.getStructuringElement(cv2.MORPH_RECT, (3,3))
    time.sleep(2)
    motor.start(30)
    
    while True:
        UpdateCamera(stream, kernel)
        
        if total == 0:
            situationBlue()
            lineDetect()
            nowPosition = avoid(nowPosition)
            
        elif total >= 0.5:
            global clock
            
            if red.area == None:
                red.area = 0.0
                
            if green.area == None:
                green.area = 0.0
            
            if red.area < green.area:
                color = "green"
                print("------")
                print("obstacle = GREEN")
                print("G area = ", green.area)
                print("R area = ", red.area)

            elif green.area < red.area:
                color = "red"
                print("------")
                print("obsacle = RED")
                print("G area = ", green.area)
                print("R area = ", red.area)

            back(nowPosition, color)
        CameraShow(stream, kernel)
            
if __name__ == '__main__':
    init()

    try:
        main()

    finally:
        fini()

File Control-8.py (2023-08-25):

import sys
import time
import math
import threading
import queue

import picamera
import picamera.array
import RPi.GPIO as GPIO

import cv2
import numpy as np
import multiprocessing as mp
from buildhat import Motor

class Camera:
    # Private
    __COLOR = "bgr"
    __USE_VIDEO_PORT = True
    __name = None
    __camera = None
    __stream = None
    
    # Public
    width = None
    height = None
    streamDatas = None
    kernel = None
    hsv = None

    # Function
    def __init__(self, name, width, height, frame, rotation = 180):
        self.__name = name
        self.width = width
        self.height = height
        self.__camera = picamera.PiCamera()
        self.__camera.resolution = (width, height)
        self.__camera.framerate = frame
        self.__camera.rotation = rotation

    def Update(self):
        self.__stream = picamera.array.PiRGBArray(self.__camera)
        self.kernel = cv2.getStructuringElement(cv2.MORPH_RECT, (3,3))
        self.__camera.capture(self.__stream, self.__COLOR, self.__USE_VIDEO_PORT)
        self.streamDatas = self.__stream.array
        self.hsv = cv2.cvtColor(self.__stream.array, cv2.COLOR_BGR2HSV)
    
    def Render(self):
        cv2.imshow(self.__name, self.__stream.array)
        cv2.waitKey(1)
        self.__stream.seek(0)
        self.__stream.truncate()

class Color:
    # Private
    __DIVISION_LINE_COLOR = (255, 215, 0)
    __DIVISION_LINE_THICKNESS = 1
    __OPENING_ITERATIONS = 1
    __colorName  = None
    __lower      = None
    __upper      = None
    __lowerOther = None
    __upperOther = None
    __outlineMethod = None

    # Public
    mask       = None
    dst        = None
    dstt       = None
    res        = None
    contour    = None
    hierarchy  = None
    maxContour = None
    area       = None
    moments    = None
    originX = None
    originY = None
    divisionDifferenceX = None
    divisionLeftX       = None
    divisionRightX      = None
    windowWidth  = None
    windowHeight = None

    # Function
    def __init__(self, colorName, lower, upper, lowerOther, upperOther, __outlineMethod, divisionDifferenceX = None, windowWidth = None, windowHeight = None):
        self.__colorName = colorName
        self.__lower = np.array(lower)
        self.__upper = np.array(upper)
        if lowerOther is not None and upperOther is not None:
            self.__lowerOther = np.array(lowerOther)
            self.__upperOther = np.array(upperOther)
        self.__outlineMethod = __outlineMethod
        self.divisionLeftX = divisionDifferenceX
        if divisionDifferenceX is not None and windowWidth is not None and windowHeight is not None:
            self.divisionRightX = windowWidth - divisionDifferenceX
            self.windowWidth = windowWidth
            self.windowHeight = windowHeight

    def Update(self, camera):
        # Masking
        if self.__colorName == "black":
            height = (camera.height, camera.height, camera.height)
            cv2.rectangle(camera.hsv, (0, 0),   (camera.width, 100),           height, -1)
            cv2.rectangle(camera.hsv, (0, 0),   (20, camera.height),           height, -1)
            cv2.rectangle(camera.hsv, (300, 0), (camera.width, camera.height), height, -1)

        self.mask = cv2.inRange(camera.hsv, self.__lower, self.__upper)
        if self.__lowerOther is not None and self.__upperOther is not None:
            maskOther = cv2.inRange(camera.hsv, self.__lowerOther, self.__upperOther)
            self.mask += maskOther
        
        # Opening
        self.dst = cv2.erode(self.mask, camera.kernel, self.__OPENING_ITERATIONS)
        self.dstt = cv2.dilate(self.dst, camera.kernel, self.__OPENING_ITERATIONS)

        # Synthesis
        self.res = cv2.bitwise_and(camera.streamDatas, camera.streamDatas, mask=self.dstt)

        # Outline
        self.contour, self.hierarchy = cv2.findContours(self.mask, cv2.RETR_EXTERNAL, self.__outlineMethod)

        # Moments and area
        if (len(self.contour) != 0):
            self.maxContour = max(self.contour, key = lambda x: cv2.contourArea(x))
            self.area = cv2.contourArea(self.maxContour)
            self.moments = cv2.moments(self.maxContour)
            if self.moments["m00"] != 0 and self.moments["m01"] != 0 and self.moments["m10"] != 0:
                self.originX = int(self.moments["m10"] / self.moments["m00"])
                self.originY = int(self.moments["m01"] / self.moments["m00"])
        else:
            self.area = None
            self.originX = None
            self.originY = None

    def Render(self):
        # DivisionLine
        if self.divisionLeftX is not None or self.divisionRightX is not None:
            windowTop = 0
            cv2.line(self.res, (self.divisionLeftX,  windowTop), (self.divisionLeftX,  self.windowHeight), self.__DIVISION_LINE_COLOR, self.__DIVISION_LINE_THICKNESS)
            cv2.line(self.res, (self.divisionRightX, windowTop), (self.divisionRightX, self.windowHeight), self.__DIVISION_LINE_COLOR, self.__DIVISION_LINE_THICKNESS)

        # Origin
        if self.originX is not None or self.originY is not None:
            cv2.circle(self.dstt, (self.originX,self.originY), 2, 100, 2, 4)
            cv2.circle(self.res, (self.originX, self.originY), 2, 100, 2, 4)
        
        # Render
        if self.res is not None:
            cv2.imshow(self.__colorName, self.res)

    def GetPositionFromColor(self, left, midle, right):
        windowLeft = 0
        # Left
        if windowLeft <= self.originX <= self.divisionLeftX:
            return left
        # Middle
        elif self.divisionLeftX <= self.originX <= self.divisionRightX:
            return midle
        # Right              
        elif self.divisionRightX <= self.originX <= self.windowWidth:
            return right
        
        print("GetPositionFromColor retutn None")
        print("divisionLeftX", self.divisionLeftX)
        print("divisionRightX", self.divisionRightX)
        print("windowWidth", self.windowWidth)
        print("originX", self.originX)

    def CanSeeColor(self):
        if self.area is not None and 500 <= self.area:
            return True

    def GetSlope(self):
        cv2.drawContours(self.res, self.maxContour, -1, (255, 0, 0), 2)

        lx, ly = (float("inf"), float("inf"))
        rx, ry = (float("-inf"), float("-inf"))
        
        if self.maxContour is not None:
            for contour in self.maxContour:
                for point in contour:
                    x = point.item(0)
                    y = point.item(1)

                    if x < lx or (x == lx and y > ly):
                        lx, ly = (x, y)

                    if x > rx or (x == rx and y > ry):
                        rx, ry = (x, y)

        if lx != float("inf") and ly != float("inf"):
            cv2.circle(self.res, (lx, ly), 5, (0, 0, 255), -1)
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

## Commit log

2023-07-01 Add files via upload
    fix
    [Control.py]
2023-08-17 Add models
    [camera2.stl, raspberry-lego-maker-plate_v4.stl, robot_under.stl]
2023-08-17 Add scheme & models
    [camera2.stl, raspberry-lego-maker-plate_v4.stl, robot_under.stl]
2023-08-19 Add files via upload
    distance trace
